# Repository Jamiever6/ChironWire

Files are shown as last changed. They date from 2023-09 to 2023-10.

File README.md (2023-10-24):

# ChironWire


The basics for this printer modification can be found at the [Voron Switchwireand](https://vorondesign.com/voron_switchwire) and [Voron Documentation](https://docs.vorondesign.com/).

My personal recommendation is to embark first on a Voron or CoreXY build. I built a Voron 2.4 and gained tons of satisfying experience and as a bonus I was left with some extra parts ;-). 

A Voron 0 will be more than enough to get the right experience and give you the possibility to print the necessary components in ABS. 

All the parts of my mod are printed in eSun ABS+ with my Voron 2.4.

I am not planning to print any ABS on this ChironWire printer!

From the Voron Switchwire you have to print the complete Gantry/XZ_Axis parts, taking care of substituting the modified files I included here. The main reason of the modification is because the Switchwire uses 30xx profiles while the Chiron has 20xx aluminum extruded profiles, so I just added 5mm to each component. Other parts are specific, depending on the electronics you will use.

In my case I used the following electronics:

[Bigtreetech Octopus Pro with TMC2209 ](https://biqu.equipment/collections/control-board/products/bigtreetech-octopus-pro-v1-0-chip-f446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) (you just need to control 3 steppers + extruder* so you can use a smaller MCU probably the best is the  Manta M5P as it doesn't need the U2C*** and has the CP1 = no need of a Raspberry Pi - ***  pls check as I am familiar only with the M8P)
U2C
[EBB SB2209 CAN ](https://biqu.equipment/collections/expansion-board/products/bigtreetech-ebb-sb2209-can-v1-0) (*the stepper for the extruder is included here)
[MINI12864 V2.0 LCD Screen](https://biqu.equipment/collections/lcd/products/bigtreetech-mini12864-v2-0-lcd-screen-rgb-backlight-mini-display-supports-marlin-diy-for-skr-3d-printer-part-1) 
Linear RAILS

Qty 5 - 12mm Linear Guide [MGN12H ](https://www.aliexpress.com/item/32829826159.html?spm=a2g0o.order_list.order_list_main.46.63281802o1rgNP)500mm 
Qty 2 - MGN12H Blocks (used for the Y to have double support) 

My sourcing reference (I am based in Sweden so the Amazon links):

Qty 2 - [10 pieces F629-2RS](https://www.amazon.se/dp/B0BZ55CZR6?ref=ppx_yo2ov_dt_b_product_details&th=1) (alternative [Aliexpress](https://www.aliexpress.com/item/1005003640031891.html?spm=a2g0o.order_list.order_list_main.35.77ff18020Tax80))
[Creality CR Touch](https://www.amazon.se/-/en/dp/B08RJ1RB13?psc=1&ref=ppx_yo2ov_dt_b_product_details) There is mod to sit the CR touch inside the Stealthburner but with the Voron Revo it seats at the same level as the nozzle so i moved it to the side. Less elegant but at least is the offset will not interfere with the printed part. Initially I thought to use TAP but realized the bed might not be strong enough for 800gr force. I am happy with the CR Touch so far given the bed is quite thin.
[NEMA14 36mm Stepper motor ](https://www.amazon.se/dp/B0BVRDGDN1?psc=1&ref=ppx_yo2ov_dt_b_product_details)for the CW2 extruder (alt [Aliexpress](https://www.aliexpress.com/item/1005005621777079.html?spm=a2g0o.order_list.order_list_main.41.63281802o1rgNP)) You can source a Stealthburner kit on Aliexpress (here just an [example](https://www.aliexpress.com/item/1005004568836712.html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))
[KEY-REAR S48K Keychain, 48"](https://www.amazon.se/dp/B002SQ9P5K?psc=1&ref=ppx_yo2ov_dt_b_product_details)
[100 Pack 2020 2040 2060 Roll in Spring Loaded T Nut m3](https://www.amazon.se/dp/B08YNFGYNH?ref=ppx_yo2ov_dt_b_product_details&th=1)
Qty 2 - [M3 * 8mm](https://www.amazon.se/dp/B08K8FQWCZ?ref=ppx_yo2ov_dt_b_product_details&th=1) socket screws 50pcs/package
[M3 Black Allen Screws](https://www.amazon.se/dp/B0BK22PWQH?ref=ppx_yo2ov_dt_b_product_details&th=1) (various lengths)
[2GT 20 Teeth 5mm Bore Timing Pulley](https://www.amazon.se/dp/B07C9X59GD?psc=1&ref=ppx_yo2ov_dt_b_product_details)
[Bipolar Stepper Motor Cables ](https://www.amazon.se/dp/B08CY46X4R?psc=1&ref=ppx_yo2ov_dt_b_product_details)1M Step XH2.54 Terminal
[E3D RapidChange Revo](https://www.amazon.se/dp/B09YQ4NWB6?ref=ppx_yo2ov_dt_b_product_details&th=1)™ Voron - 1.75mm, 24V
[Cooling Fan DC 24V 50x50x15mm ](https://www.amazon.se/dp/B07NSVP7YG?psc=1&ref=ppx_yo2ov_dt_b_product_details)5015
[GT2 timing belt 6mm x 5m ](https://www.amazon.se/-/en/non-slip-upgrade-suitable-printers-belt-drive/dp/B09XJW2ZRC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)(I had a Ruthex already but cant find where I bought it)

**Disassembly and assembly steps**

1. remove all existing electronics 
2. remove the bed 



3. if you want to achieve the full 400mm Y travel with the Stealthburner head you can move the Z columns 30mm backward drilling new holes to the frame (I haven't done it as atm I am OK having max Y travel 375mm)
4. invert the T-supports for the Z frame as they will interfere with the new motor supports XZ  
5. now it is a good time as any to install the X & Z stepper motors withe their motor_mount assembled (just snug the screws and lose the tensioner all the way)
6. install the upper idler assemblies
7. Y carriage modification
- don't forget to clean and lubricate the bearings of the rails (check YT tutorials)
- install the Y rails adding the 2nd rail block (be careful with derailing).
- connect the 3 pieces composing the Y carriage frame using the leftover 8mm spacers 
- sketch the hole pattern for the rails blocks (20x20mm) and space them 30mm
- punch for drilling 
- bolt together the trapezoidal parts and drill them at the same time (I used a 3.5-3,8mm drill to have some extra clearance). De-burr the holes
- bolt together the Y carriage frame and check that the heated bed fits. Mine was slightly off and just enlarged the 4 holes where the bed screws and springs sit.
- once you have installed the Y carriage frame check that the Y stop clicks. As mine was just on the edge I just added one of the original Z stop metal pieces while clamping the blocks connecting the Y belt.







8. install the Z rails all the way up against the upper z_carriage_stops (keep the plastic rails stoppers to avoid derailing) and the bottom z_carriage_stop + keyback assembly
9. **at this point there is no turning back to the old Chiron as we start Cutting**!!!
- Cut the X 2020 alu profile to 510mm 
- Cut the X rail to 467mm (I used a Dremel diamond disk)
10. install the XZ_blocks and make sure later that the belts are not touching the X alu profile





11. assemble the z_bearing_blocks (left and generic) to the X alu 2020 and bolt them to the Z carriage
12. install the Stealthburner head
13. cut the 5m GT2 belt in two. You need to shorten them few cm so you have around 5-6cm left each side for later be able to grab the pair and tension it. Do a test install and cut it (check YT tutorials, the 2 belts MUST be exactly the same length - teeth on teeth and slide them though your hands without skipping teeth, measure twice and get them right)
14. install the belts and tension them lightly (the extra length can be folded inside the X carriage). 
15. install the MCU, Raspberry Pi, U2C and the existing 800W(!) PU using the PU_support_1 and _2 and the existing metal bracket (edit 2023-09-24). I did not use the secondary 24V PU



16. install a fan 24V 60x60 using the printed support (one works fine with my setup) 
17. Now that the mechanical is done it is time to start wiring it all together (check [Github ](https://github.com/Jamiever6?tab=repositories)for most of the schematics of the electronics)
18. I attached as an example the printer.cfg file. I still have few things to sort out like the beeper and small issues but it is fully functional as soon as you have installed klipper, flashed the firmware, etc. etc. etc.
19. finish up with the spooler holder and if you want to have the tube like in mine, print the included bowden_retainer from the Voron 2.4
CREDITS: 

Voron awesome community, [github](https://github.com/VoronDesign)

[Revo nozzle holder ](https://www.printables.com/model/248325-revo-nozzle-holder)by Jan

[Angle bracket 90 ° ](https://www.thingiverse.com/thing:3409079)by Eternauta74

[2020 V-Slot Aluminium Extrusion Profile ](https://www.thingiverse.com/thing:5181722)by chris_kwng

[Raspberry Pi Camera Mount ](https://www.thingiverse.com/thing:4761307)by crsn00

USA chiron-voron-switchwire-parts-list by TheDarkSoul97

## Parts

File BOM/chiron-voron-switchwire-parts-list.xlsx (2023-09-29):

Chiron Voron Switchwire Parts List
 | Type | Object | Cost | Link
Electronics | Board | Bigtreetech Octopus Pro | $81.48 | https://biqu.equipment/collections/control-board/products/bigtreetech-octopus-pro-v1-0-chip-f446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
 | U2C | U2C V2.1 | $17.02 | https://biqu.equipment/products/bigtreetech-ebb-sb2209-can-v1-0?variant=40214284468322
 | EBB | EBB SB2209 CAN | $25.68 | https://biqu.equipment/collections/expansion-board/products/bigtreetech-ebb-sb2209-can-v1-0
 | LCD | MINI12864 V2.0 LCD Screen | $12.68 | https://biqu.equipment/collections/lcd/products/bigtreetech-mini12864-v2-0-lcd-screen-rgb-backlight-mini-display-supports-marlin-diy-for-skr-3d-printer-part-1
 |  | Electronic Total: | $136.86
 | Type | Object | Cost | Link
Linear Rails | Rail | 12mm Linear Guide (500mm) x5 | $89.95 | https://www.aliexpress.us/item/2251832643511407.html
 | Block | Rail Blocks x2 | $13.72 | https://www.aliexpress.us/item/2251832643511407.html
 |  | Rail Total: | $103.67
 | Type | Object | Cost | Link | a
Mechanical Hardware | Bearing | Flanged Groove Ball Bearings x2 | $6.40 | https://www.aliexpress.us/item/3256803453717139.html | a
 | T-Nut | 100 Pack 2020 2040 2060 Roll in Spring Loaded T Nut m3 | $16.68 | https://www.amazon.com/100-Pack-Aluminum-Extrusions-Profile-Accessories/dp/B08YNFGYNH?s=industrial | a
 | Screw | M3*8mm Socket Screws 100 Pc | $7.86 | https://www.amazon.com/Socket-Screws-Bolts-Thread-100pcs/dp/B07CMQ1SQH?s=industrial | a
 | Screw | M3 Black Allen Screws Assortment | $23.39 | https://www.amazon.com/sspa/click | a
 | Pulley | GT2 20 Teeth 5mm Bore Timing Pulley | $6.99 | https://www.amazon.com/WINSINN-Aluminum-Synchronous-Timing-Printer/dp/B077GNZK3J?s=industrial | a
 | Belt | GT2 timing belt 6mm x 5m | $10.99 | https://www.amazon.com/Upgrade-Non-Slip-Version-Printer-Printers/dp/B08R93QQ8Z | a
 | Fan | Cooling Fan DC 24V 50x50x15mm | $9.99 | https://www.amazon.com/SoundOriginal-50x50x15mm-Humidifier-Aromatherapy-Replacement/dp/B0755BY9RH | a
 | Hotend | E3D RapidChange Revo | $95.99 | https://www.amazon.com/Genuine-E3D-Assembly-1-75mm-REVO-VORON-175-24V-AS/dp/B09YQ74ZKZ | a
 | Cable | Bipolar Stepper Motor Cables | $9.99 | https://www.amazon.com/sspa/click | a
 | Motor | NEMA14 36mm Stepper motor | $12.46 | https://www.aliexpress.us/item/3256805435462327.html
 | Leveler | Creality CR Touch | $39.00 | https://www.amazon.com/Professional-Auto-Leveling-Specially-Designed/dp/B0979F7RWN | a
 | Keychain | KEY-REAR S48K Keychain, 48" | $16.81 | https://www.amazon.com/KEY-BAK-SUPER48-Ambidextrous-Retractable-Locking/dp/B07FJG4ZLB?s=industrial | a
 |  | Mechanical Hardware Total: | $256.55 |  | a
 |  |  |  |  | a
 |  | Grand Total: | $497.08

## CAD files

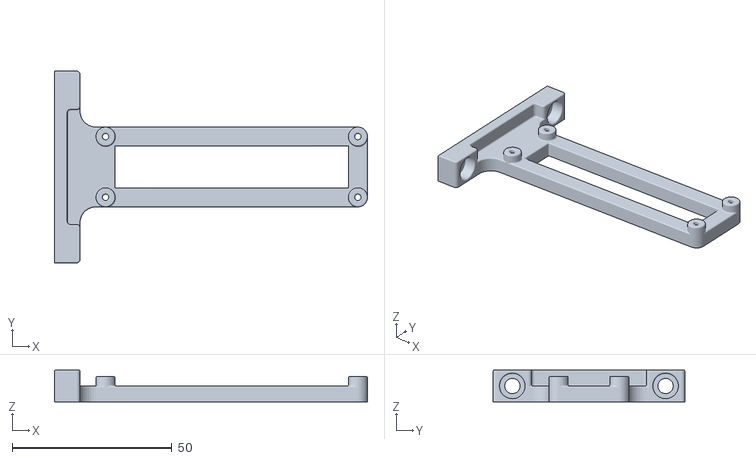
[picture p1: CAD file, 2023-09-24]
STL/U2C support v3.stl
98.0 x 60.0 x 10.0

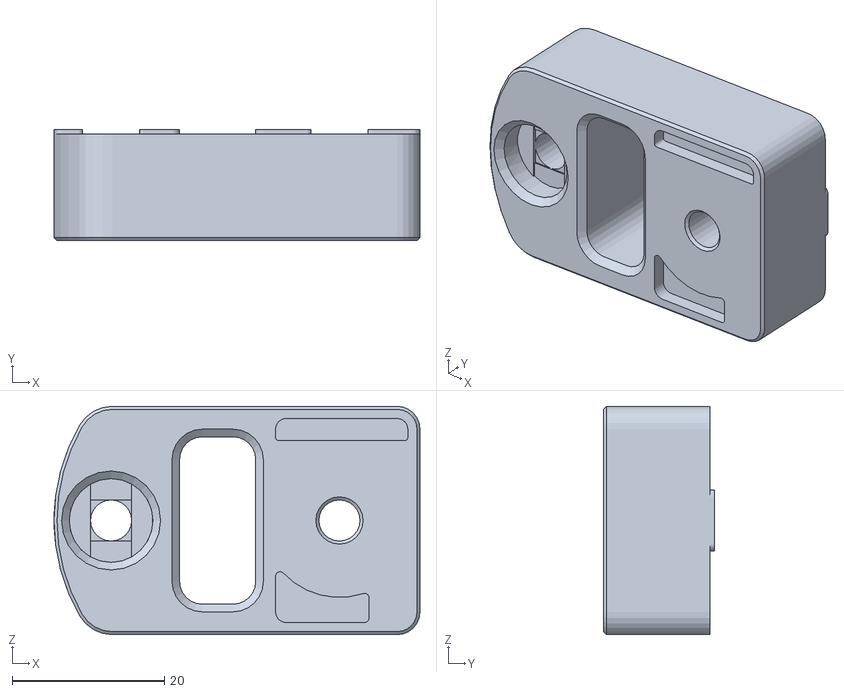
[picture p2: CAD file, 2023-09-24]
STL/Switchwire_Upper block right_Chiron_v1.stl
48.1 x 14.6 x 30.0

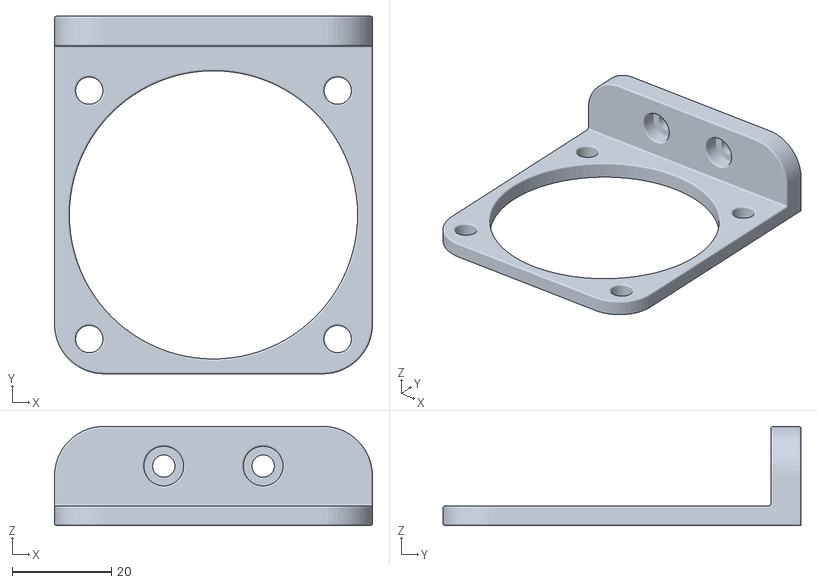
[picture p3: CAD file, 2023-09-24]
STL/Fan NF-A6x25 support 4020 profile v1.stl
64.0 x 72.0 x 20.0

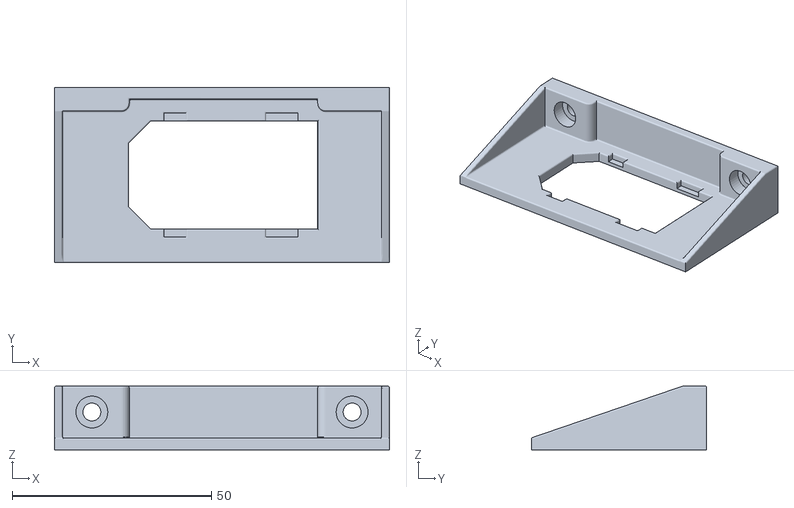
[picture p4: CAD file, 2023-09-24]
STL/Inlet Power Socket IEC320 C14 v2.stl
84.0 x 44.0 x 16.0

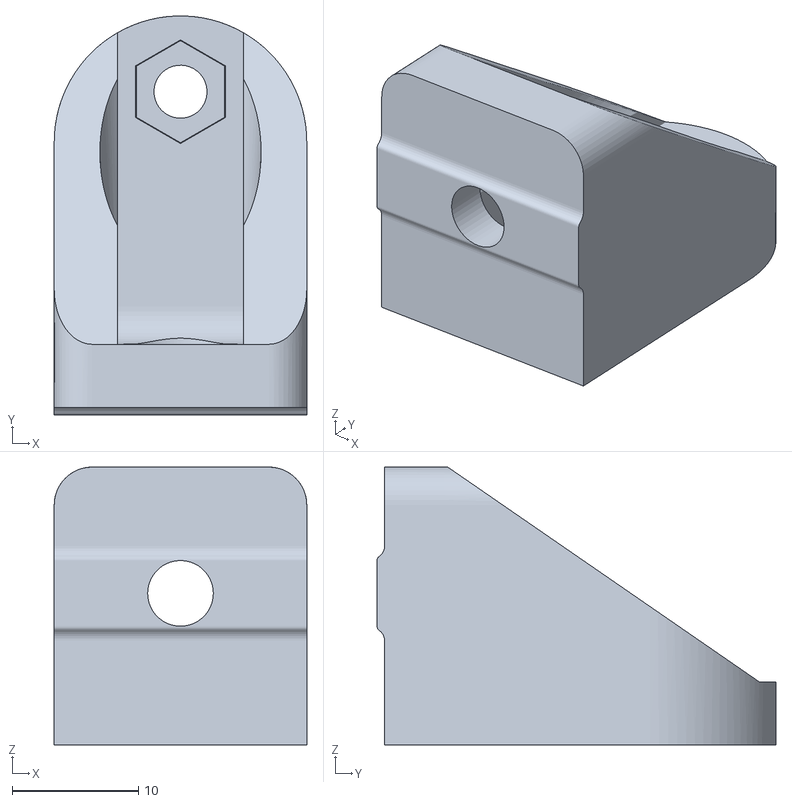
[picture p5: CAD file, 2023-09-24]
STL/PU support 1 v4.stl
20.0 x 31.6 x 22.0

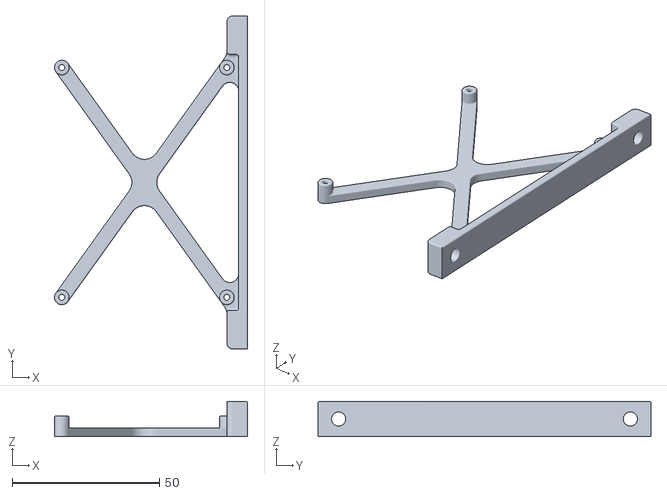
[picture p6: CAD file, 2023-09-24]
STL/Bed_heater_support v2.stl
65.5 x 113.0 x 12.0

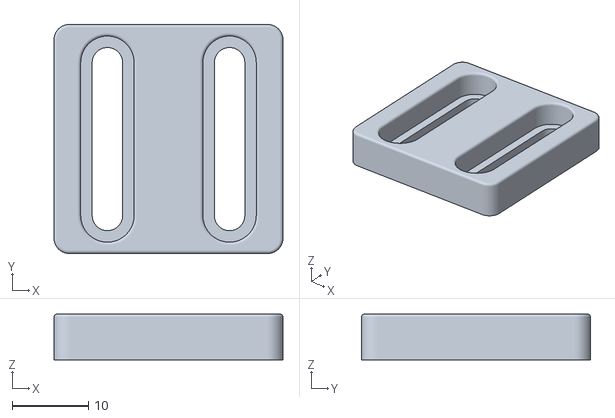
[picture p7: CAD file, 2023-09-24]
STL/Y_stop v1_optional.stl
30.0 x 30.0 x 6.00

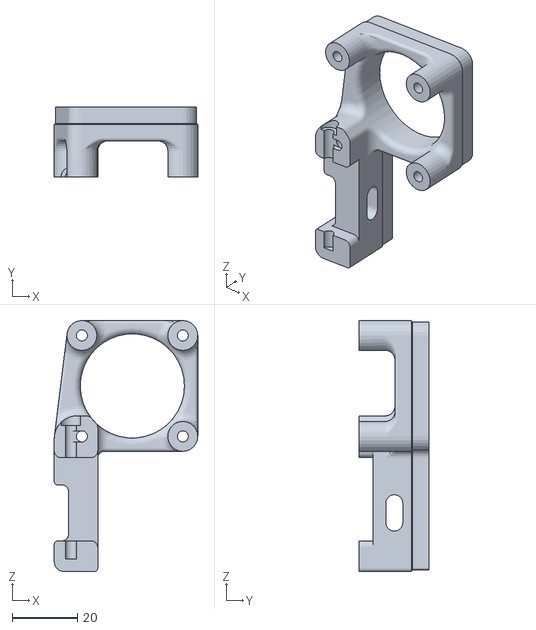
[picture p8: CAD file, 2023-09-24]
STL/Switchwire_X motor_Chiron_v1.stl
44.1 x 21.4 x 77.1

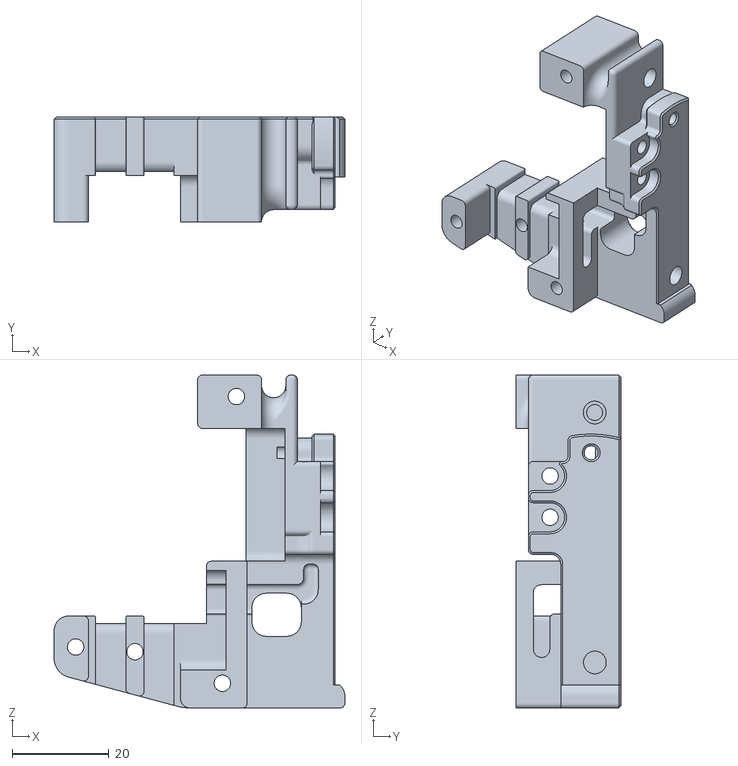
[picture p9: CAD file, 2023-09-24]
STL/SW_Carriage_Right v7.stl
60.0 x 21.6 x 68.8

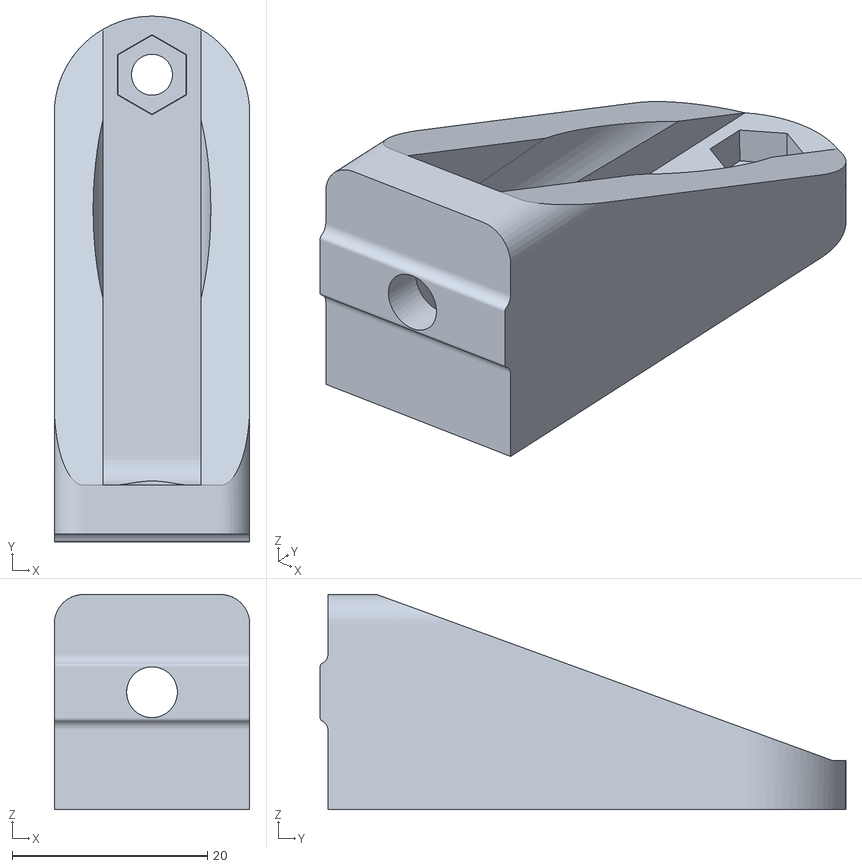
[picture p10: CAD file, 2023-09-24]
STL/PU support 2 v3.stl
20.0 x 53.8 x 22.0

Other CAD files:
STL/Switchwire_upper block left_Chiron_v1.stl
STL/Switchwire_Z motor_Chiron_v1.stl
CAD/Bed_heater_support v2.f3d
CAD/Fan NF-A6x25 support 4020 profile v1.f3d
CAD/Inlet Power Socket IEC320 C14 v2.f3d
CAD/PU support 1 v4.f3d
CAD/PU support 2 v3.f3d
CAD/SW_Carriage_Right v7.f3d
CAD/U2C support v3.f3d
CAD/Y_stop v1_optional.f3d

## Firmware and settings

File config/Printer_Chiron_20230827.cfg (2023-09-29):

[include fluidd.cfg]
[include stealthburner_leds.cfg]
[virtual_sdcard]
path: /home/pi/printer_data/gcodes
on_error_gcode: CANCEL_PRINT

###KLIPPER CONFIG FOR MODIFIED ANYCUBIC CHIRON (VORON SWITCHWIRE STEALTHBURNER-CW2 CAN-BUS)###

###MCUs###

[include mainsail.cfg]
[mcu]
serial: /dev/serial/by-id/YOUR_MCUID

[mcu EBBCan]
canbus_uuid: YOURCANBUS_UUID

[temperature_sensor SoC]
sensor_type: temperature_host

[temperature_sensor MCU]
sensor_type: temperature_mcu

###------------------------------------###
###           KINEMATICS               ###
###------------------------------------###

[printer]
kinematics: corexz
max_velocity: 400
max_accel: 4000
max_z_velocity: 30
max_z_accel: 200

[safe_z_home]
home_xy_position: 200,200
speed: 60
z_hop: 10
z_hop_speed: 20

###------------------------------------###
#           EBB 2209                   ###
###------------------------------------###

[temperature_sensor EBB_NTC]
sensor_type: Generic 3950
sensor_pin: EBBCan: PA2

[adxl345]
cs_pin: EBBCan: PB12
spi_software_sclk_pin: EBBCan: PB10
spi_software_mosi_pin: EBBCan: PB11
spi_software_miso_pin: EBBCan: PB2
axes_map: z,-y,x

[resonance_tester]
probe_points: 200, 200, 20
accel_chip: adxl345

[extruder]
step_pin: EBBCan: PD0
dir_pin: !EBBCan: PD1
enable_pin: !EBBCan: PD2
microsteps: 32
##	rotation_distance = <previous_rotation_distance> * <actual_extrude_distance> / 100
##  22.6789511 is a good starting point
rotation_distance: 21.998356	#Bondtech 5mm Drive Gears
gear_ratio: 50:10				#BMG Gear Ratio
full_steps_per_rotation: 200	#200 for 1.8 degree, 400 for 0.9 degree
nozzle_diameter: 0.400
filament_diameter: 1.750
heater_pin: EBBCan: PB13
sensor_type: ATC Semitec 104NT-4-R025H42G
sensor_pin: EBBCan: PA3
#control: pid
#pid_Kp: 21.527
#pid_Ki: 1.063
#pid_Kd: 108.982
min_temp: 15
max_temp: 250

# sensor_type:MAX31865
# sensor_pin: EBBCan: PA4
# spi_bus: spi1
# rtd_nominal_r: 100
# rtd_reference_r: 430
# rtd_num_of_wires: 2

[tmc2209 extruder]
uart_pin: EBBCan: PA15
run_current: 0.650
stealthchop_threshold: 999999

[fan]
##	Print Cooling Fan - CNC_FAN2
pin: EBBCan: PA1
kick_start_time: 0.5
##	Depending on your fan, you may need to increase this value
##	if your fan will not start. Can change cycle_time (increase)
##	if your fan is not able to slow down effectively
off_below: 0.10

[heater_fan hotend_fan]
##	hot end - CNC_FAN1
pin: EBBCan: PA0
heater: extruder
heater_temp: 50.0

#[heater_fan 4W_FAN0]
#pin: EBBCan: PB14
#tachometer_pin: EBBCan: PB15
#tachometer_ppr: 1

#[neopixel hotend_rgb]
#pin: EBBCan:PD3

## NPN and PNP proximity switch types can be set by jumper
#[probe]
#pin: ^EBBCan: PC13

#[output_pin PB5]
#pin: EBBCan: PB5

#[output_pin PB7]
#pin: EBBCan: PB7

#[output_pin PB6]
#pin: EBBCan: PB6

###STEPPERS###

### THESE ARE KNOWN GOOD VALUES FOR STOCK STEPPERS AND DRIVERS SHOULD NOT NEED TO BE MODIFIED.

[stepper_x]
#Motor 0
step_pin: PF13
dir_pin: PF12
enable_pin: !PF14
microsteps: 16
rotation_distance: 40
endstop_pin: EBBCan: PB6
full_steps_per_rotation: 200  #set to 400 for 0.9 degree stepper
position_min: 0
position_endstop: 407 #check your measurement
position_max: 407 #check your measurement
homing_speed: 80   #Max 100
homing_retract_dist: 5
homing_positive_dir: true

[tmc2209 stepper_x]
uart_pin: PC4
interpolate: True
run_current: 0.8
sense_resistor: 0.110
stealthchop_threshold: 0

[stepper_z]
#Motor 2
step_pin: PF11
dir_pin: PG3
enable_pin: !PG5
microsteps: 16
rotation_distance: 40
Full_steps_per_rotation = 200
endstop_pin: probe:z_virtual_endstop
position_min: -1
position_max: 400
homing_speed: 20.0

[tmc2209 stepper_z]
uart_pin: PC6
interpolate: True
run_current: 0.8
sense_resistor: 0.110
stealthchop_threshold: 0

[stepper_y]
#Motor 1
step_pin: PG0
dir_pin: PG1
enable_pin: !PF15
microsteps: 16
rotation_distance: 32
Full_steps_per_rotation = 200
#step_distance: .01
endstop_pin: ^!PG9
position_min: -30
position_endstop: -30
position_max: 375 #keeping the Z profiles in the original Chiron position
homing_speed: 80.0

[tmc2209 stepper_y]
uart_pin: PD11
interpolate: True
run_current: 0.8
sense_resistor: 0.110
stealthchop_threshold: 0


###-------------------------###
###           BED           ###
###-------------------------###

[heater_bed]
heater_pin: PA3
sensor_type: EPCOS 100K B57560G104F
sensor_pin: PF3
#control: pid
#pid_Kp: 67.675
#pid_Ki: 1.920
#pid_Kd: 596.390
min_temp: 10
max_temp: 120 
pwm_cycle_time: 0.2 #EUfrequency

[bed_mesh]
speed: 150
horizontal_move_z: 10
mesh_min: 60,60
mesh_max: 340, 340
probe_count: 5,5

[heater_fan controller_fan]
pin: PD12
max_power: 1.0
shutdown_speed: 0.0
kick_start_time: 5.0
heater: heater_bed
heater_temp: 18
fan_speed: 0.4

###MISC###

###----------------------------------------------###
###                     LEDS                     ###
###----------------------------------------------###

[neopixel case_leds]
pin: PB0
#chain_count: 6
#color_order: GRB
#initial_RED: 1
#initial_GREEN: 1
#initial_BLUE: 1

[gcode_arcs]
resolution: 1.0

[display_status]

###----------------------------------------------###
###                   CR Touch                   ###
###----------------------------------------------###

[bltouch]
sensor_pin: EBBCan: PB8
control_pin: EBBCan: PB9
x_offset: 36
y_offset: 19
#z_offset: 2.01
speed: 20.0

[board_pins]
aliases:
    # EXP1 header
    EXP1_1=PE8, EXP1_2=PE7,
    EXP1_3=PE9, EXP1_4=PE10,
    EXP1_5=PE12, EXP1_6=PE13,    # Slot in the socket on this side
    EXP1_7=PE14, EXP1_8=PE15,
    EXP1_9=<GND>, EXP1_10=<5V>,

    # EXP2 header
    EXP2_1=PA6, EXP2_2=PA5,
    EXP2_3=PB1, EXP2_4=PA4,
    EXP2_5=PB2, EXP2_6=PA7,      # Slot in the socket on this side
    EXP2_7=PC15, EXP2_8=<RST>,
    EXP2_9=<GND>, EXP2_10=PC5

# See the sample-lcd.cfg file for definitions of common LCD displays.

#####################################################################
# 	Displays
#####################################################################

## 	Uncomment the display that you have
#--------------------------------------------------------------------

#[display]
##	RepRapDiscount 128x64 Full Graphic Smart Controller
#lcd_type: st7920
#cs_pin: EXP1_4
#sclk_pin: EXP1_5
#sid_pin: EXP1_3
#menu_timeout: 40
#encoder_pins: ^EXP2_5, ^EXP2_3
#click_pin: ^!EXP1_2

#[output_pin beeper]
#pin: EXP1_1

#--------------------------------------------------------------------

[display]
#	mini12864 LCD Display
lcd_type: uc1701
cs_pin: EXP1_3
a0_pin: EXP1_4
rst_pin: EXP1_5
encoder_pins: ^EXP2_5, ^EXP2_3
click_pin: ^!EXP1_2
contrast: 63
spi_software_miso_pin: EXP2_1
spi_software_mosi_pin: EXP2_6
spi_software_sclk_pin: EXP2_2

[neopixel btt_mini12864]
#	To control Neopixel RGB in mini12864 display
pin: EXP1_6
chain_count: 3
initial_RED: 0.1
initial_GREEN: 0.5
initial_BLUE: 0.0
color_order: RGB

##	Set RGB values on boot up for each Neopixel. 
##	Index 1 = display, Index 2 and 3 = Knob
[delayed_gcode setdisplayneopixel]
initial_duration: 1
gcode:
       SET_LED LED=btt_mini12864 RED=0.5 GREEN=0.5 BLUE=0 INDEX=1 TRANSMIT=0
       SET_LED LED=btt_mini12864 RED=0.5 GREEN=0.5 BLUE=0 INDEX=2 TRANSMIT=0
       SET_LED LED=btt_mini12864 RED=0.5 GREEN=0.5 BLUE=0 INDEX=3 

 
######################################################################
# Filament Change
######################################################################

# M600: Filament Change. This macro will pause the printer, move the
# tool to the change position, and retract the filament 50mm. Adjust
# the retraction settings for your own extruder. After filament has
# been changed, the print can be resumed from its previous position
# with the "RESUME" gcode.

[pause_resume]

[gcode_macro PARK_MACRO]
#default_parameter_X: 0.0
#default_parameter_Y: -85
#default_parameter_Z: 30
gcode:
 #       M117 Parking..
        G91
        G1 E-20 F1500
        G1 Z{Z}
        G90
        G1 X{X} Y{Y} F3000

[gcode_macro PAUSE_MACRO]
gcode:
        M117 Pause activated
        PAUSE
        PARK_MACRO
        SET_IDLE_TIMEOUT TIMEOUT=999999

# Pause/Resume functionality with support of position capture and restore
[pause_resume]
recover_velocity: 40

[gcode_macro M600]
gcode:
    {% set X = params.X|default(50)|float %}
    {% set Y = params.Y|default(0)|float %}
    {% set Z = params.Z|default(10)|float %}
    SAVE_GCODE_STATE NAME=<M600_State>
    PAUSE
    SET_IDLE_TIMEOUT TIMEOUT=999999
    G91
    G1 E-.8 F2700
    G1 Z{Z}
    G90
    G1 X{X} Y{Y} F3000
    G91
    G1 E-30 F1000
    RESTORE_GCODE_STATE NAME=<M600_State>
    
    ###FILAMENT RUNOUT
    
[filament_switch_sensor FSensor]
pause_on_runout: True
runout_gcode:M600 
insert_gcode: M117 RunOut False
event_delay: 8.0
switch_pin: ^!PG11

[output_pin beeper]
pin: EXP1_1
value: 0
shutdown_value: 0
pwm: True
cycle_time: 0.0005 ; Default beeper tone in kHz. 1 / 0.0005 = 2000Hz (2kHz)   

###################
###   MACROS    ###
###################

#MESH
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

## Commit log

2023-09-24 added PU supports
    [PU support 1 v4.f3d, PU support 2 v3.f3d]
2023-09-24 STL files
    [Bed_heater_support v2.stl, Fan NF-A6x25 support 4020 profile v1.stl, Inlet Power Socket IEC320 C14 v2.stl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]
2023-09-24 Create STL
